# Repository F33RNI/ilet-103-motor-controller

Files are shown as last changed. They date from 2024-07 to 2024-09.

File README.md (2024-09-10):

# ➿ ilet-103-motor-controller

## Digital speed controller for ILET 103 reel-to-reel deck | Цифровой контроллер скорости ленты катушечного магнитофона ИЛЕТЬ 103

----------

## ❓ Что это

Данный репозиторий содержит инструкцию по переделке катушечного магнитофона на примере ИЛЕТЬ 103-1 для добавления цифровой регулировки скорости, замены асинхронного двигателя на двигатель постоянного тока, роликовой передачи на пассик, а также, исходный код контроллера с ПИД-регулятором скорости.

Кроме ИЛЕТЬ 103-1, данная переделка возможна **для любых других катушечных магнитофонов** с подобным устройством и принципом работы.

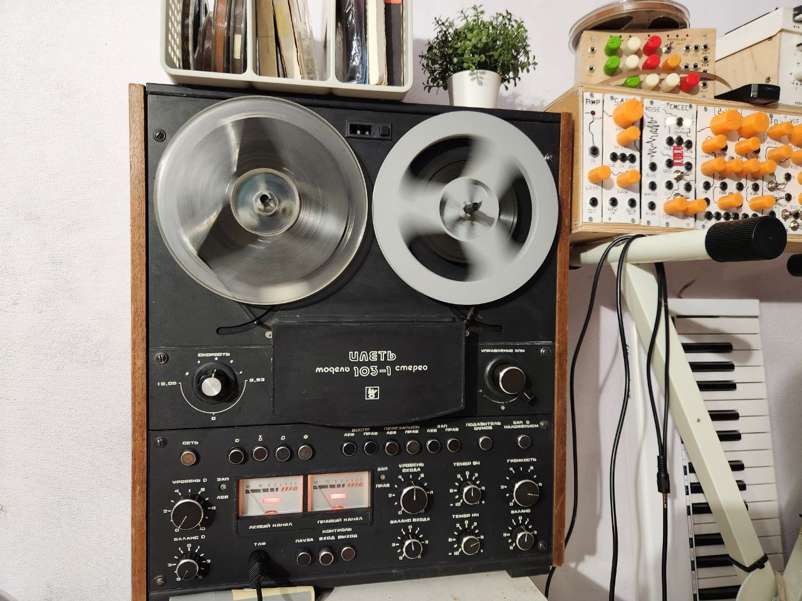
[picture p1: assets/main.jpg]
ИЛЕТЬ 103-1


----------

## ⚠️ Дисклеймер

> Авторка репозитория не несёт ответственности за любой причинённый моральный / материальный / физический или иной ущерб, связанный с использованием данного репозитория / кода / 3д-моделей / схем / иных других материалов. Вы всё делаете на свой страх и риск!
> Сетевое напряжение может быть **смертельно**!

----------

## 🔧 Замена двигателя и роликового привода на пассик, сборка контроллера

### Контроллер двигателя

1. Подберите мощный двигатель постонного тока. Например, от старого принтера. Обычно для питания таких двигателей можно использовать блок питания напряжением 24V и током не менее 2А.

> ВАЖНО ⚠️: Для питания двигателя используйте отдельный экранированный блок питания, PEN проводник которого необходимо соединить с общим корпусом магнитофона и сетевым проводником PEN.

2. На заднюю часть двигателя установите готовый или самодельный оптический энкодер. Я использовала самодельный энкодер, содержащий 4 чёрных и 4 белых сегмента;
3. Соберите контроллер, используя схему ниже:
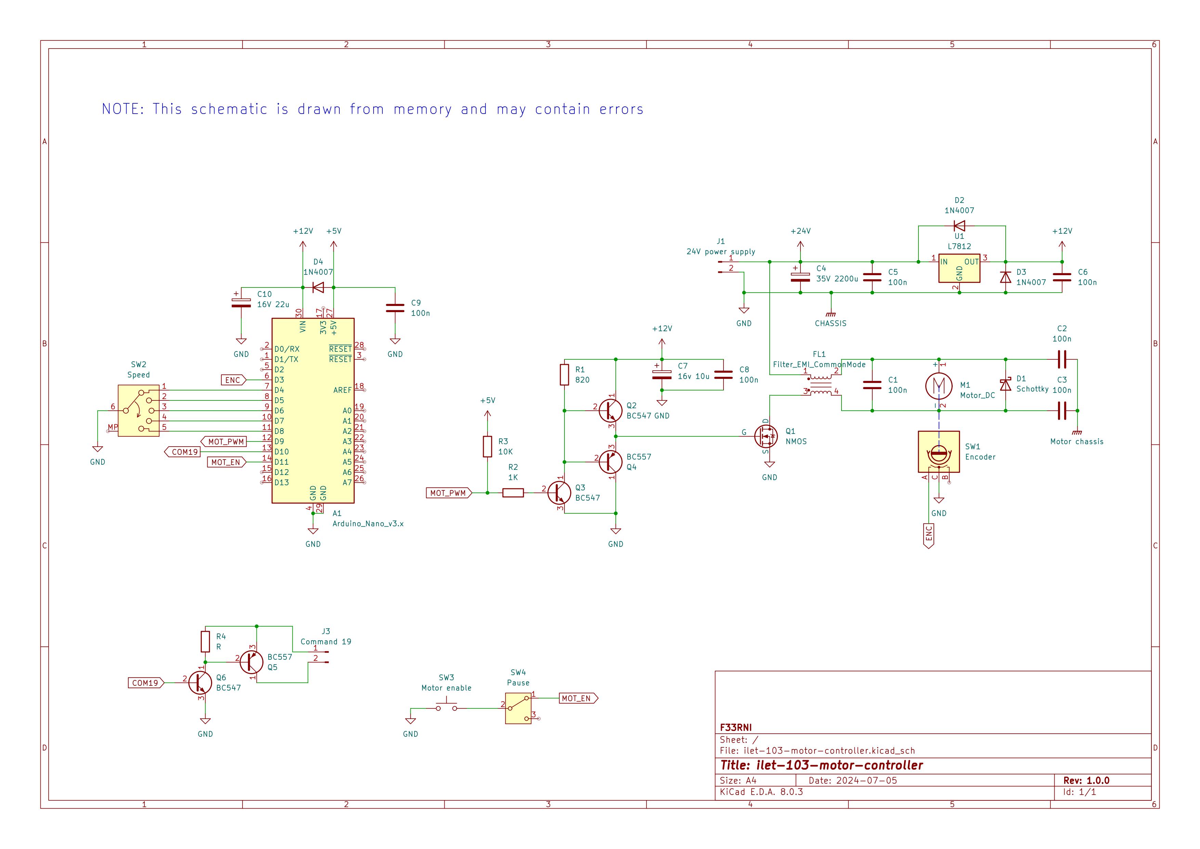
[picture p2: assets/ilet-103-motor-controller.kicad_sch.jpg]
Схема контроллера
  

4. Собранный и установленный контроллер и мотор должны выглядеть следующим образом:
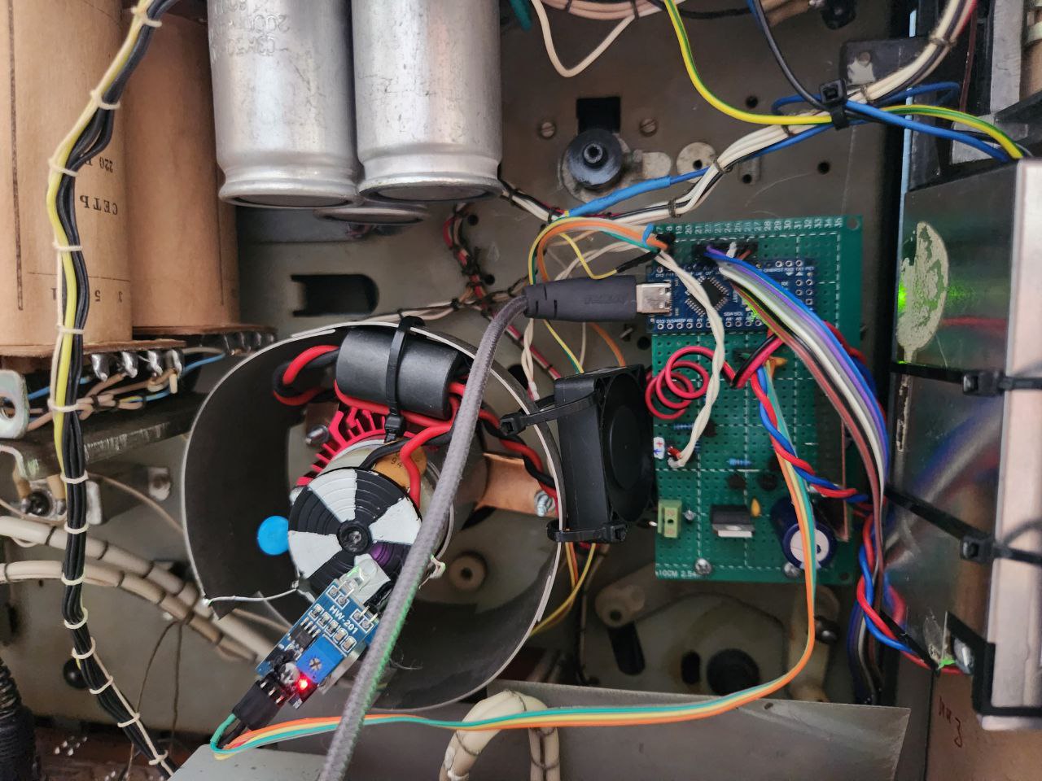
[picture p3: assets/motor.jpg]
Установленный мотор и плата контроллера
  

> Ваши компоненты, их номиналы и т.д. могут отличаться. Экспериментируйте!

Ниже представлены фото подключенного переключателя включения мотора и переключателя скорости. Переключатель паузы подключен последовательно с кнопкой включения мотора

> ВАЖНО ⚠️: Отключите и заизолируйте от переключателя паузы все остальные провода, т.к. на них высокий потенциал!

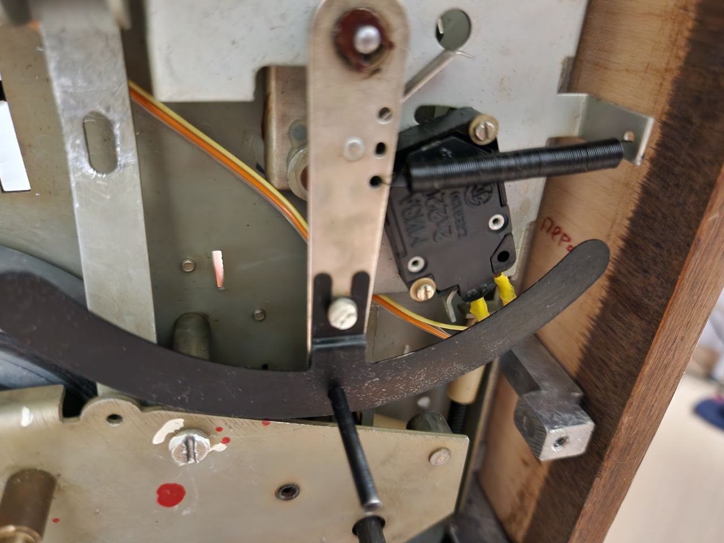
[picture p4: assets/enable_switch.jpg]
Включение мотора
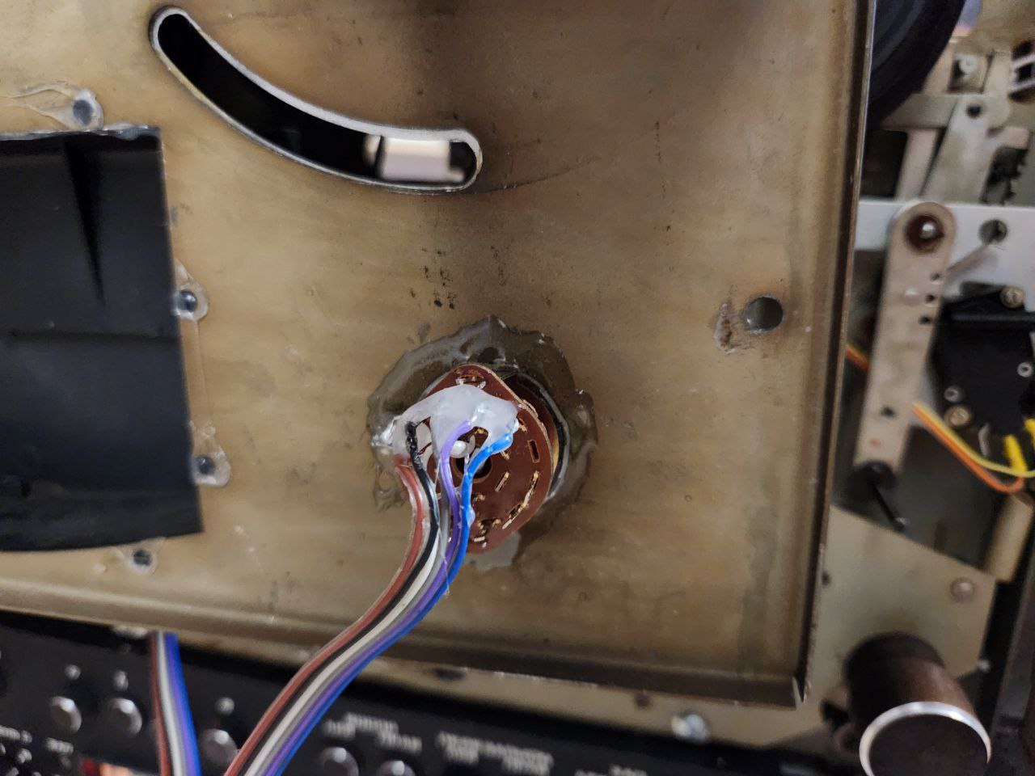
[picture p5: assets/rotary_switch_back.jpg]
Переключатель скорости
|  |  |
|---|---|

> Если в процессе работы мотор нагревается, можно установить небольшой кулер

### Шкив и пассик вместо роликового привода

> В ИЛЕТЬ 103-1 изначально крайне шумный привод капстана. Чтобы убрать шум (также, после установки контроллера и мотора постоянного тока необходимости в механическом изменении скорости нет), необходимо заменить привод на пассик, в качестве которого можно отрезать 8-10мм диэлектрической перчатки

1. Распечатайте на 3Д-принтере или изготовьте иным образом детали шкива `3d/ILET103-Top.stl` и `3d/ILET103-Bottom.stl`;
2. Соберите шкив, как показано на фото ниже:

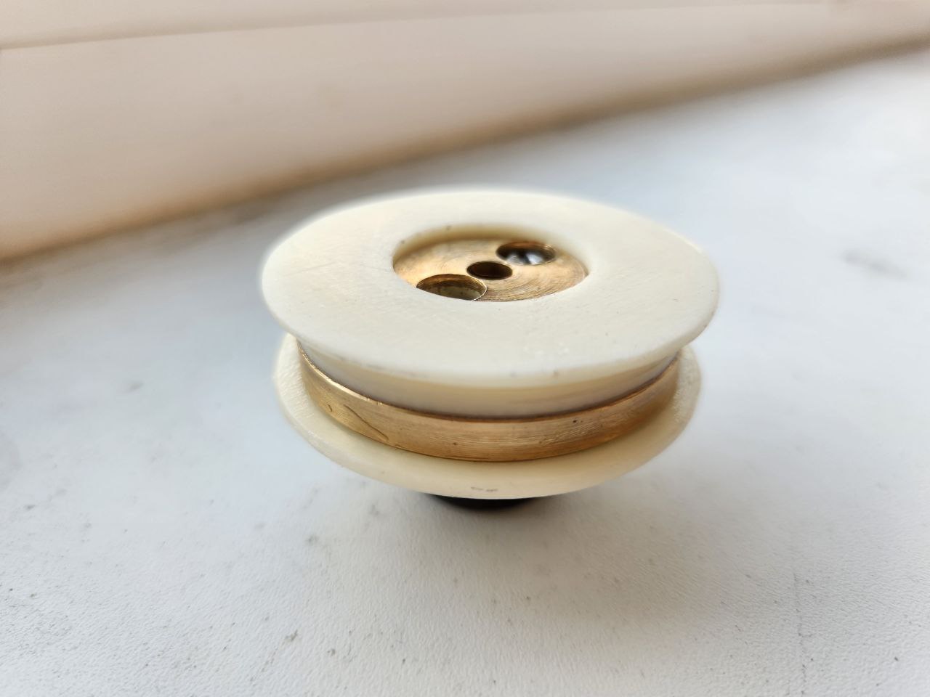
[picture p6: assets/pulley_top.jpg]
Шкив в сборе, вид сверху
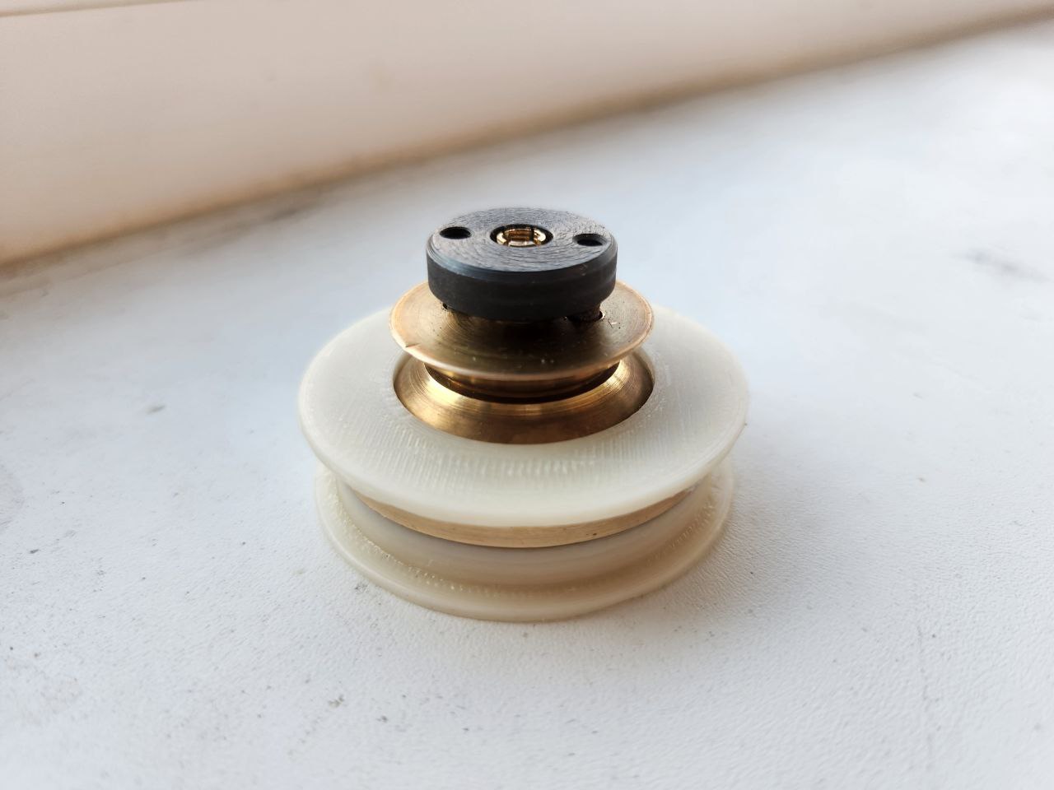
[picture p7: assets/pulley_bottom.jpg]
Шкив в сборе, вид снизу
|  |  |
|---|---|

3. Отключите и уберите электромагнит паузы
4. Установите пассик:
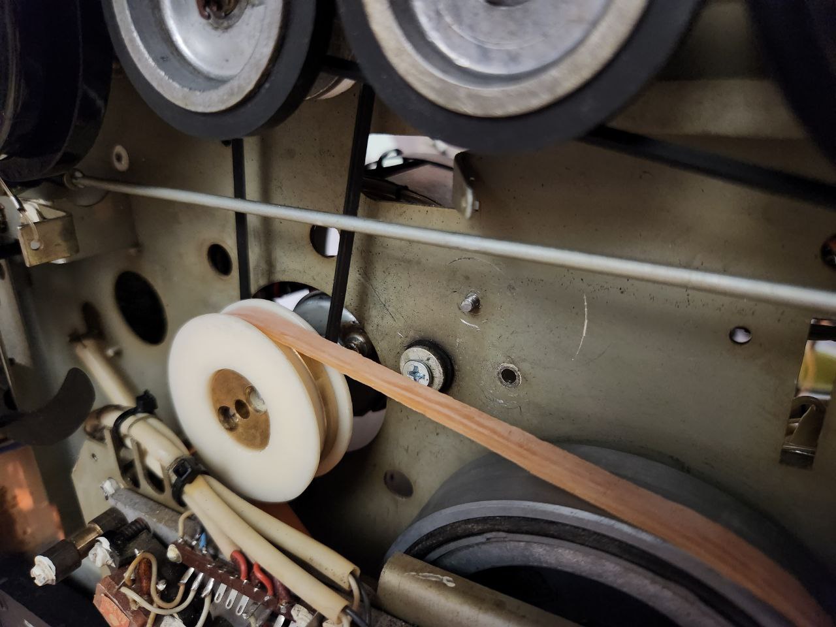
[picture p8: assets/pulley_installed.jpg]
Пассик


----------

## 🏗️🟠 Сборка при помощи PlatformIO

1. Клонируйте репозиторий с модулями:

  ```shell
  git clone --recursive https://github.com/F33RNI/ilet-103-motor-controller.git
  cd ilet-103-motor-controlle
  ```

- IDE версия:
  - Откройте репозиторий `ilet-103-motor-controller` в IDE и запустите сборку.

- Консольная версия (PlatformIO Core):

  ```shell
  pio run
  ```

----------

## 🏗️🔵 Сборка при помощи Arduino IDE / arduino-cli

1. Клонируйте репозиторий с модулями:

  ```shell
  git clone --recursive https://github.com/F33RNI/ilet-103-motor-controller.git
  cd ilet-103-motor-controlle
  ```

- IDE версия
  - Откройте файл `ilet-103-motor-controller.ino` в IDE, выберите нужную платформу и запустите сборку.

- Консольная версия (arduino-cli)

  - Создайте директорию `build`:

  ```shell
  mkdir build
  ```

  - Запустите сборку (заменив `arduino:avr:uno` на требуюмую платформу):

  ```shell
  arduino-cli compile --verbose --build-path ./build -b arduino:avr:uno ilet-103-motor-controller.ino
  ```

----------

## ⚙️ Настройка контроллера и ПИД-регулятора

- Все настройки находятся в файле `include/config.h`
- Настройки портов находятся в файле `include/pins.h`

Если, указанные в настройках, параметры ПИД не подошли для вашей сборки, настройте ПИД вручную. Для этого:

> К сожалению, автоматическая настройка PID-регулятора методом Циглера-Никольса не подходит для данного проекта, хотя,
> можете попробовать. Для этого, обратитесь к документации библиотеки [PetalPID](https://github.com/F33RNI/PetalPID)

1. Включите режим `DEBUG`. Используйте любую программу плоттера последовательного порта, чтобы следить за графиками скорости;
2. Установите все параметры в 0 (`PID_P_GAIN = 0.f`, `PID_I_GAIN = 0.f` и `PID_D_GAIN = 0.f`);
3. Установите среднюю скорость;
4. Постепенно повышайте `PID_P_GAIN` до тех пор, пока не начнутся осцилляции;
5. Уменьшите `PID_P_GAIN` до тех пор, пока осцилляции не пропадут полностью и ещё немного;
6. Увеличьте `PID_I_GAIN` так, чтобы скорость достигалась максимально быстро без осцилляций;
7. Плавно повышайте `PID_D_GAIN`, `PID_P_GAIN` и `PID_I_GAIN`, стараясь добиться максимальной стабильности и скорости реакции.

----------

## ✨ Участие в разработке

1. Клонируйте репозиторий с модулями:

  ```shell
  git clone --recursive https://github.com/F33RNI/ilet-103-motor-controller.git
  ```

2. При редактиовании / добавлении кода, следуйте стилю, указанному в `.clang-format`;
3. При создании коммитов, используйте стиль [Conventional Commits](https://www.conventionalcommits.org/en/v1.0.0/#specification>)
4. Создайте пул-реквест.

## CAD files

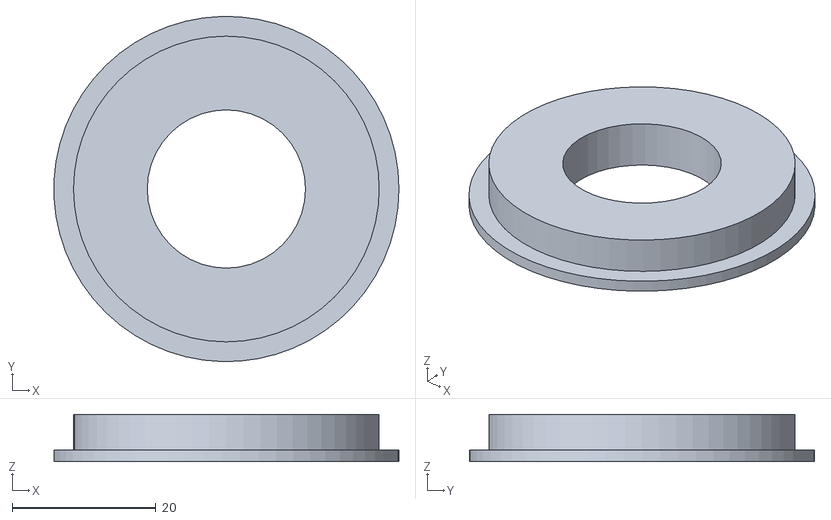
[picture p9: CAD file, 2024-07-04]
3d/ILET103-Top.stl
48.0 x 48.0 x 6.60

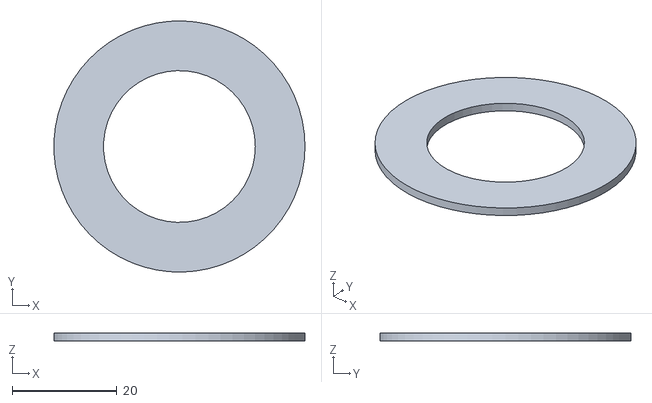
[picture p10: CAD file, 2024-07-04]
3d/ILET103-Bottom.stl
48.0 x 48.0 x 1.60

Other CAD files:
3d/ILET103.FCStd

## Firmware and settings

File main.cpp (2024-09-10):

/**
 * @file ilet-103-motor-controller.ino
 * @author Fern Lane
 * @brief Digital speed controller for ILET 103 reel-to-reel deck
 *
 * @copyright Copyright (c) 2024 Fern Lane
 *
 * This file is part of the ilet-103-motor-controller distribution.
 * See <https://github.com/F33RNI/ilet-103-motor-controller> for more info.
 *
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
 * You should have received a copy of the GNU Affero General Public License
 * long with this program.  If not, see <http://www.gnu.org/licenses/>.
 */

#include <Arduino.h>

// For official Arduino IDE compatibility. Don't need to include .cpp for PlatformIO
#ifndef PLATFORMIO_STYLE_IMPORTS
#include "lib/PetalPID/src/PetalPID.cpp"
#endif
#include "lib/PetalPID/src/PetalPID.h"

#include "include/config.h"
#include "include/pins.h"

#include "include/encoder.h"
#include "include/motor.h"
#include "include/rotary_switch.h"

boolean motor_enabled_prev;

PetalPID pid = PetalPID();

void setup() {
    // Setup encoder
    encoder.init();

    // Setup rotary switch as pullup pins
    for (uint8_t i = 0; i < sizeof(SPEED_SELECTOR_PINS) / sizeof(uint8_t); ++i)
        pinMode(SPEED_SELECTOR_PINS[i], INPUT_PULLUP);

    // Setup enable
    pinMode(MOTOR_ENABLE_PIN, INPUT_PULLUP);

    // Setup command 19
    pinMode(COMMAND_19_PIN, OUTPUT);
#ifdef COMMAND_19_INVERTED
    digitalWrite(COMMAND_19_PIN, HIGH);
#endif

    // Setup PID motor
    pid.set_min_max_output(PID_MIN_OUT, PID_MAX_OUT);
    pid.set_min_max_integral(PID_MIN_INTEGRAL, PID_MAX_INTEGRAL);
    pid.set_gains(PID_P_GAIN, PID_I_GAIN, PID_D_GAIN);
    Motor::init();

    // Setup serial port for debugging
#ifdef DEBUG
    Serial.begin(115200);
#endif

    // Wait a bit to make sure everything is settled
    delay(100);
}

void loop() {
    // Read rotary switch
    float rpm_setpoint_raw = rotarySwitch.read_setpoint();

    // Enable / disable command 19 according to RPM
    boolean command_19 = rpm_setpoint_raw > RPM_SETPOINTS[sizeof(RPM_SETPOINTS) / sizeof(float) / 2];
#ifdef COMMAND_19_INVERTED
    digitalWrite(COMMAND_19_PIN, !command_19);
#else
    digitalWrite(COMMAND_19_PIN, command_19);
#endif

    // Check if we're stalled
    boolean is_stalled = encoder.stall_check();

// Check if we need to enable or disable motor
#ifdef MOTOR_ENABLED_INVERTED
    boolean motor_enabled = !digitalRead(MOTOR_ENABLE_PIN);
#else
    boolean motor_enabled = digitalRead(MOTOR_ENABLE_PIN);
#endif

    // Something changed -> reset setpoint and PID
    if (motor_enabled != motor_enabled_prev) {
        rotarySwitch.reset();
        pid.reset();
        Motor::write(0.f);

        // Stop or resume encoder
        if (motor_enabled)
            encoder.resume();
        else
            encoder.stop();
    }

    // Save for the next cycle
    motor_enabled_prev = motor_enabled;

    // We don't need other encoder and pid actions now
    if (!motor_enabled)
        return;

    // If we have encoder callback or stalled
    if (encoder.get_triggered() || is_stalled) {
        // Clear triggered flag
        encoder.clear_triggered();

        // Filter setpoint
        float rpm_setpoint_filtered = rotarySwitch.filter_setpoint();

        // Calculate PID only if motor is enabled
        if (motor_enabled)
            Motor::write(pid.calculate(encoder.get_rpm_filtered(), rpm_setpoint_filtered, micros()));

        // Reset PID if motor is disabled
        else
            pid.reset();

// Plot debug info (only if motor is spinning or stalled)
#ifdef DEBUG
        Serial.print(rpm_setpoint_filtered);
        Serial.print("\t");
        Serial.println(encoder.get_rpm_filtered());
#endif
    }

    // Simulate encoder cycle if stalled
    if (is_stalled) {
        uint64_t period_min = (1.f / (ENCODER_MIN_RPM / 60.f * ENCODER_DIVIDER)) * 1.e6;
        delay(period_min / 1000);
        delayMicroseconds(period_min % 1000);
    }
}

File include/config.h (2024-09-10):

/**
 * @file config.h
 * @author Fern Lane
 * @brief PWM, PID-controller and other configs
 *
 * @copyright Copyright (c) 2024 Fern Lane
 *
 * This file is part of the ilet-103-motor-controller distribution.
 * See <https://github.com/F33RNI/ilet-103-motor-controller> for more info.
 *
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
 * You should have received a copy of the GNU Affero General Public License
 * long with this program.  If not, see <http://www.gnu.org/licenses/>.
 */

#ifndef CONFIG_H__
#define CONFIG_H__

#include <Arduino.h>

// Uncomment to receive rpm_setpoint_filtered and rpm_filtered separated by tab (/t) at 115200
#define DEBUG

// In microseconds (1 / (21us / 1000 / 1000) ~= 47619Hz)
const uint64_t MOTOR_PWM_PERIOD = 21UL;

// Encoder ticks per revolution
const float ENCODER_DIVIDER = 4.f;

// Consider RPM as 0 if it's below this value
const float ENCODER_MIN_RPM = 100.f;

// Main low-pass filter. Closer to 1 = smoother and slower
// Actual filter value will be RPM_FILTER / time_delta (in seconds)
// RPM_FILTER = K * (1 / (RPS * ENCODER_DIVIDER))
const float RPM_FILTER = .85f * (1.f / ((1443.76f / 60.f) * ENCODER_DIVIDER));

// Low-pass filter for smoothing setpoint change. Closer to 1 = smoother and slower
const float SETPOINT_FILTER = .94;

// Rotary switch setpoints. Must be the same size as SPEED_SELECTOR_PINS
// RPM @ 6mm: (IPS * 25.4 / (pi * 6 mm)) * 60, RPM @ 100 mm / 42.5 mm: (IPS * 25.4 / (pi * 6 mm)) * 60 * (100 / 42)
// <https://en.wikipedia.org/wiki/Audio_tape_specifications>
// Standard IPS: 1.875, 3.75, 7.5 -> motor RPMs: 360.94, 721.88, 1443.76
const float RPM_SETPOINTS[] = {360.94f, 541.41f, 721.88f, 1082.82f, 1443.76f};

// PID values
const float PID_P_GAIN = .0012f;
const float PID_I_GAIN = .0036f;
const float PID_D_GAIN = .000002f;

// Integral part of the PID will be clamped to this range to prevent integral windup
const float PID_MIN_INTEGRAL = -1000.f;
const float PID_MAX_INTEGRAL = 1000.f;

// Output of the PID will be clamped to this range
const float PID_MIN_OUT = 0.f;
const float PID_MAX_OUT = .8f;

#endif

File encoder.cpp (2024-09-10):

/**
 * @file encoder.cpp
 * @author Fern Lane
 * @brief Encoder RPM meter
 *
 * @copyright Copyright (c) 2024 Fern Lane
 *
 * This file is part of the ilet-103-motor-controller distribution.
 * See <https://github.com/F33RNI/ilet-103-motor-controller> for more info.
 *
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
 * You should have received a copy of the GNU Affero General Public License
 * long with this program.  If not, see <http://www.gnu.org/licenses/>.
 */

#include <Arduino.h>
#include <util/atomic.h>

#include "include/config.h"
#include "include/pins.h"

#include "include/encoder.h"

// Preinstantiate
Encoder encoder;

/**
 * @brief Sets up encoder pin and connects interrupt callback
 */
void Encoder::init(void) {
    pinMode(ENCODER_PIN, INPUT_PULLUP);
    attachInterrupt(digitalPinToInterrupt(ENCODER_PIN), isr, ENCODER_INTERRUPT_MODE);
    is_interrupt_attached = true;
}

/**
 * @brief Interrupt callback (encoder)
 * Calculates motor speed in RPM. Call check_triggered() to check for new cycle
 */
void Encoder::handle_interrupt(void) {
    uint64_t time_ = micros();

    // micros() overflow
    if (time_prev == 0 || time_prev >= time_) {
        time_prev = time_;
        return;
    }

    // Calculate time between callbacks (encoder period) in seconds
    time_delta = (float) (time_ - time_prev) / 1.e6f;
    time_prev = time_;

    // Calculate unfiltered rpm
    float rpm_raw = (1.f / time_delta) / ENCODER_DIVIDER * 60.f;

    // First time -> don't filter
    if (rpm_filtered == 0.f)
        rpm_filtered = rpm_raw;
    else {
        // Calculate filter with variable cycle time
        float filter_k = RPM_FILTER / time_delta;
        if (filter_k < 0.f)
            filter_k = 0.f;
        else if (filter_k > FILTER_MAX)
            filter_k = FILTER_MAX;

        // Filter it
        rpm_filtered =
            rpm_filtered * filter_k + rpm_raw * (1.f - filter_k) / 2.f + rpm_raw_prev * (1.f - filter_k) / 2.f;
    }
    rpm_raw_prev = rpm_raw;

    // Set triggered flag
    triggered = true;
}

/**
 * @brief Checks if no interrupts in a long time and slowly brings rpm_filtered to 0
 * and time_delta to the actual time delta
 * Call it in a main loop() before everything (before calling clear_triggered())
 *
 * @return boolean true if stalled
 */
boolean Encoder::stall_check(void) {
    uint64_t time_current = micros();

    float time_prev_;
    ATOMIC_BLOCK(ATOMIC_RESTORESTATE) { time_prev_ = time_prev; }

    // Ignore if interrupt is set or time is incorrect
    if (get_triggered() || time_prev_ > time_current) {
        // Fix time
        if (time_prev_ > time_current) {
            noInterrupts();
            time_prev = time_current;
            interrupts();
        }

        return false;
    }

    boolean stalled = false;

    float time_delta_test = (float) (time_current - time_prev_) / 1.e6f;
    if ((1.f / time_delta_test) / ENCODER_DIVIDER * 60.f < ENCODER_MIN_RPM) {

        // Disable interrupts to prevent errors
        noInterrupts();

        // Set variables
        rpm_filtered *= .98f;
        time_delta = time_delta_test;
        stalled = true;

        // Enable interrupts back
        interrupts();
    }

    return stalled;
}

/**
 * @brief Detaches interrupts and sets time_prev to current micros() and time_delta and rpm_filtered to 0
 */
void Encoder::stop(void) {
    // Detach encoder interrupts
    if (is_interrupt_attached) {
        noInterrupts();
        detachInterrupt(digitalPinToInterrupt(ENCODER_PIN));
        is_interrupt_attached = false;
        interrupts();
    }

    time_prev = micros();
    time_delta = 0.f;
    rpm_filtered = 0.f;
}

/**
 * @brief Attaches encoder interrupt and sets time_prev to current micros() and time_delta and rpm_filtered to 0
 */
void Encoder::resume(void) {
    // Attach back
    if (!is_interrupt_attached) {
        attachInterrupt(digitalPinToInterrupt(ENCODER_PIN), isr, ENCODER_INTERRUPT_MODE);
        is_interrupt_attached = true;
    }

    time_prev = micros();
    time_delta = 0.f;
    rpm_filtered = 0.f;
}

/**
 * @return float current RPM (filtered)
 */
float Encoder::get_rpm_filtered(void) {
    float rpm_filtered_;
    ATOMIC_BLOCK(ATOMIC_RESTORESTATE) { rpm_filtered_ = rpm_filtered; }
    return rpm_filtered_;
}

/**
 * @return boolean true if encoder triggered
 * Call clear_triggered() to reset it
 */
boolean Encoder::get_triggered(void) {
    boolean triggered_;
    ATOMIC_BLOCK(ATOMIC_RESTORESTATE) { triggered_ = triggered; }
    return triggered_;
}

/**
 * @brief Sets triggered to false (clears triggered flag)
 */
void Encoder::clear_triggered(void) {
    // Ignore if not triggered to prevent errors
    if (!get_triggered())
        return;
    triggered = false;
}

/**
 * @brief Static interrupt callback (wrapper for handle_interrupt())
 */
void Encoder::isr(void) { encoder.handle_interrupt(); }

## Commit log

2024-07-01 fix: invert command 19
    [main.cpp]
2024-07-04 style: Arduino IDE compatibility
2024-07-04 style: proper naming and Arduino IDE compatibility
2024-07-04 feat: add 3d models, schematic, photos and docs
    [ILET103-Bottom.stl, ILET103-Top.stl, ILET103.FCStd]
2024-09-10 chore: switch to PetalPID

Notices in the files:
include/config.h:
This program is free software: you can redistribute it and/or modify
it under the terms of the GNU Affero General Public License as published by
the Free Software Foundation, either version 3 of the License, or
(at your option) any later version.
